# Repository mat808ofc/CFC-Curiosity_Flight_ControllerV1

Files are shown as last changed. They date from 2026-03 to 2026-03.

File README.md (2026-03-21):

# CFC (Curiosity's Flight Controller)

### About

This is a flight controller with USB-C, a Micro-SD card reader, a battery charger, servos, a pressure sensor, a IMU, a GNSS Module and voltage sensing via ADC. It was originally designed for model rockets but it can be used for planes too. I took inspiration from the @NotARoomba SFC guide, but designed it myself and this is my own creation.

### INSPIRATION:

This is my second project and first stasis project. Since I want to follow aerospace engineering, i chose to build a flight controller. I followed the @NotARoomba guide and built it from scratch. I added a GNSS Module for auto pilot and Voltage Sensing via ADC to know when the battery is getting low. I want to use this in my custom built RC plane. I really liked building everything although some things were a real pain.

### CHALLENGES:

My biggest challenge was routing the PCB, when I routed it for the first time the board was way too big to fit on the plane and way too expensive. So after that I significantly reduced the board size and made it the smallest it can get and the cheapest. In between that, I had to change a lot of pins and inputs in STM32CubeMX so that the routing wouldn't be an absolute mess, and that took a really long time and absolutely drained my patience and mental power.

### BOM:
| Name | Purpose | Cost (USD) | Qty | Total (USD) | Link | Distributor |
|---|---|---|-----|---|---|---|
| PCBA (1 board)  | The actual flight controller | $140 | 1 | $140 | https://www.elecrow.com/ | Elecrow |

Total estimated cost: $140

### Extras:

This project does not need a case or anything 3D printed or designed, it will be inside a RC plane.
If you have any questions, DM me on slack: Mateus (mateus.flecha808)

## Schematic

### USB-C & Crystals
{BE57653B-7D3A-48C3-BE49-C0519F7B529C}

### Decoupling, Buttons & Servos
{79CEA256-14AA-4DC2-861F-85EBC9C6EA1F}

### Battery Charger & STM32
{32F101CB-92D8-42CC-A244-E05E275E72F9}

### Pressure Sensor & Micro-SD
{E111CCD5-0065-440A-B6FF-7CA9D5AE25CE}

### Power & GNSS
{53D61D9F-42BA-49DF-AC49-1D3BC913D2A1}

### IMU
{816D461F-DD70-45E3-AB0F-E9185D550F2D}

### All
{09707E38-BBC4-4B8D-BA47-B80D99204EBA}

---

## PCB


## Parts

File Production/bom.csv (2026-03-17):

Designator | Footprint | Quantity | Value | LCSC Part #
C1, C3, C6, C7, C8, C9, CNEXTTOTEN1 | 0805 | 7 | 10uF
C10, C15, C18, C19, C25, C26, C27, C28, C29, C38, C42, C43, C45 | 0805 | 13 | 100nF
C11, C24 | 0402 | 2 | 2.2uF
C12, C13, C14, C16, C17 | 0805 | 5 | 22uF
C2 | 0805 | 1 | 44uF
C20 | 0805 | 1 | 10nF
C21, C23 | 0402 | 2 | 0.1uF
C22 | 0402 | 1 | 2.2nF
C30, C31, C32, C33, C44 | 0402 | 5 | 1uF
C34, C35 | 0805 | 2 | 20pF
C36, C37 | 0402 | 2 | 6.8pF
C4 | 0805 | 1 | 1uF
C5 | 0805 | 1 | 47nF
CARD1 | TF-SMD_TF-01A | 1 | TF-01A | C91145
D1 | 0402 | 1 | LED
J1 | TerminalBlock_Xinya_XY308-2.54-2P_1x02_P2.54mm_Horizontal | 1 | Screw_Terminal_01x02
J2, J3 | PinHeader_1x03_P2.54mm_Vertical | 2 | Conn_01x03
L1 | L2520 | 1 | 1uH
L2 | IND-SMD_L4.0-W4.0-A | 1 | 1.5uH
L3 | IND-SMD_L3.0-W3.0 | 1 | 5.6uH
L4 | L0603 | 1 | FCM1608KF-601T03 | C141723
R1, R2 | 0402 | 2 | 5.1K
R10, R12, R13, R16, R17, R18, R19, R20, R21, R24, R27, R3, R4, R5, R6, R7 | 0402 | 16 | 10K
R11 | 0402 | 1 | 30.1K
R14 | 0402 | 1 | 100K
R15 | 0402 | 1 | 22.1K
R22, R23 | 0402 | 2 | 4.7K
R25 | 0805 | 1 | 200K
R26 | 0805 | 1 | 100K
R8 | 0402 | 1 | 383
R9 | 0402 | 1 | 5.23K
SW1, SW2 | SW-SMD_L3.9-W3.0-P4.45 | 2 | TS-1088-AR02016 | C720477
U1 | VFQFPN-24_L4.0-W4.0-P0.50-BL-EP2.8 | 1 | BQ25883RGER | C544362
U2 | LQFP-64_10x10mm_P0.5mm | 1 | STM32F722RET6
U3 | InvenSense_QFN-24_4x4mm_P0.5mm | 1 | MPU-6050
U4 | VQFN-15_L3.0-W2.5-P0.50-BL | 1 | TPS63070RNMR | C109322
U5 | SOT-23-6 | 1 | LMR51430
U6 | LGA-10_L2.0-W2.0-P0.50-TL_BMP580 | 1 | BMP580 | C22391138
U8 | ublox_SAM-M8Q | 1 | SAM-M8Q
USB1 | USB-C-SMD_TYPE-C-6PIN-2MD-073 | 1 | TYPE-C 16PIN 2MD(073) | C2765186
X1 | CRYSTAL-SMD_4P-L3.2-W2.5-BL | 1 | X322525MOB4SI | C9006
X2 | FC-135R_L3.2-W1.5 | 1 | Q13FC1350000400 | C32346

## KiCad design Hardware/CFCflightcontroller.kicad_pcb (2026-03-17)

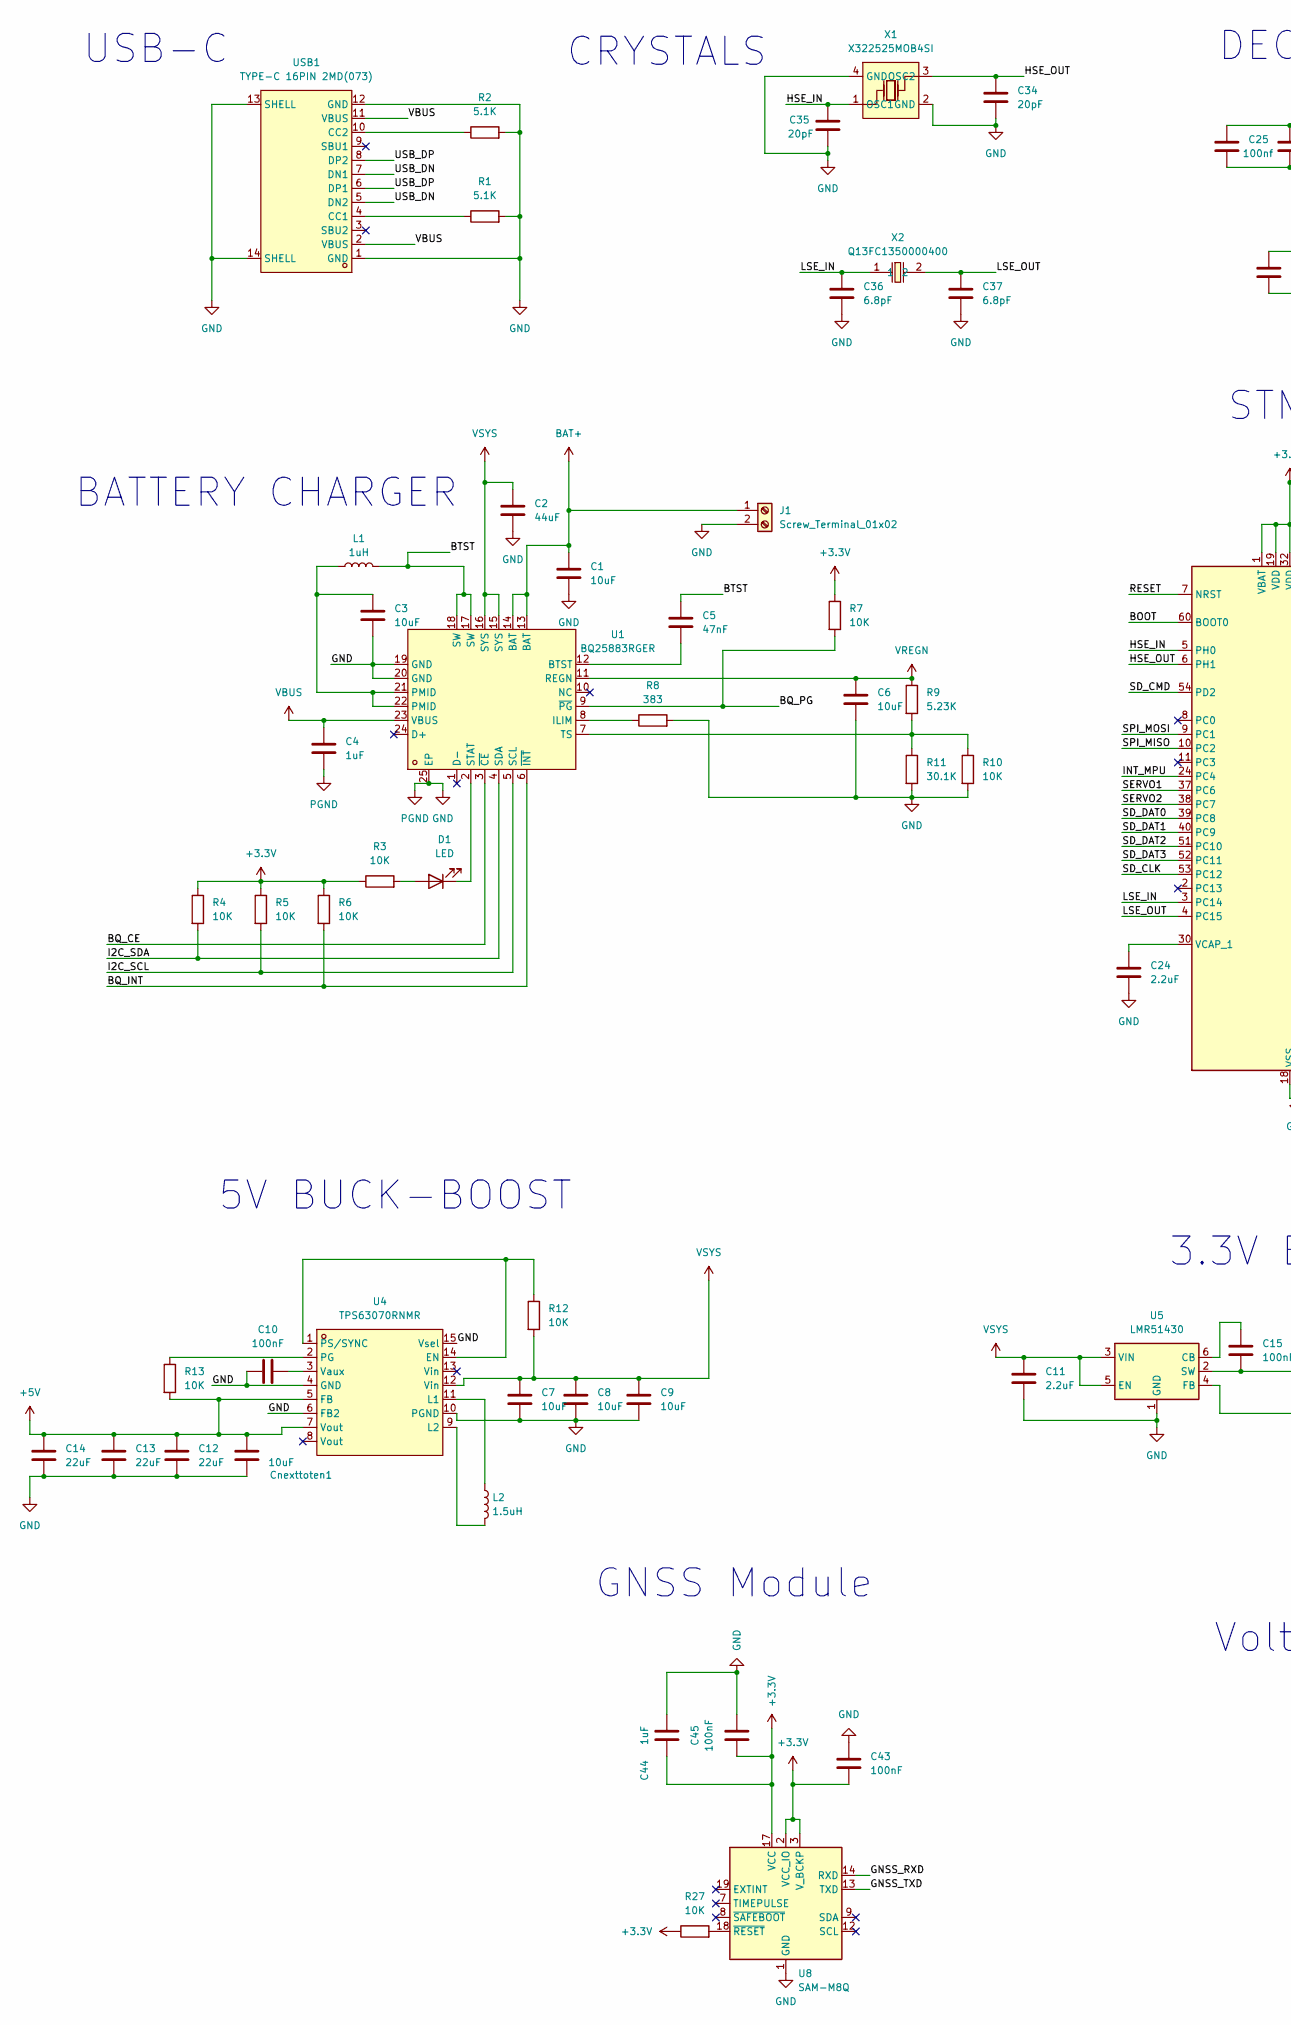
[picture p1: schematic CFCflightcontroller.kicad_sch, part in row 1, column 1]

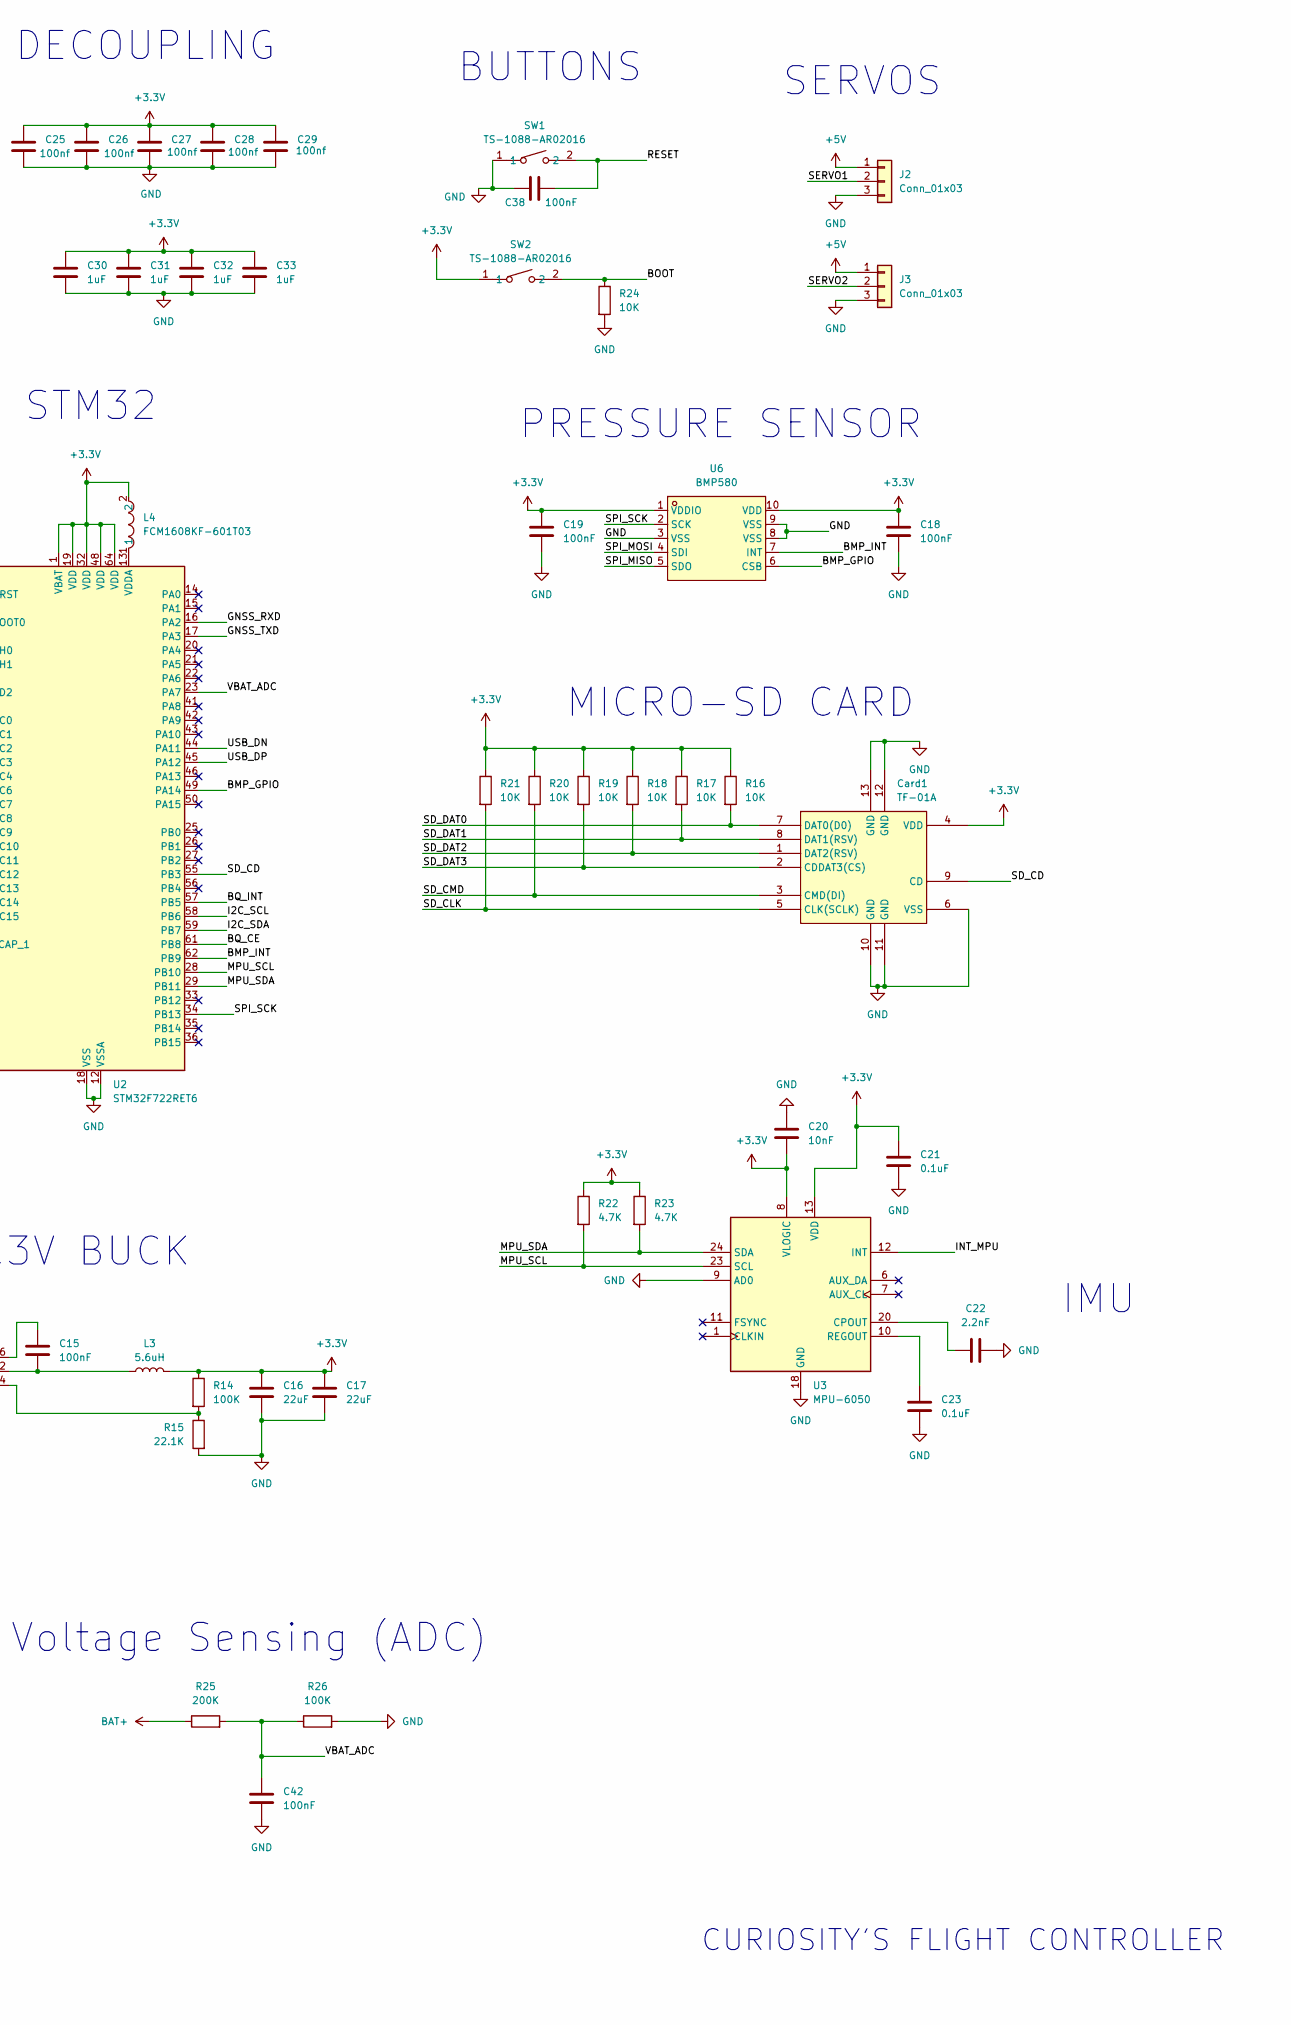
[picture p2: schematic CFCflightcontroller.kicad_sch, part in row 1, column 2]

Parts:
C1, C3, C6, C7, C8, C9: 10uF; C_0805_2012Metric
C2: 44uF; C_0805_2012Metric
C4: 1uF; C_0805_2012Metric
C5: 47nF; C_0805_2012Metric
C10, C15, C18, C19, C38, C42, C43, C45: 100nF; C_0805_2012Metric
C11, C24: 2.2uF; C_0402_1005Metric
C12, C13, C14, C16, C17: 22uF; C_0805_2012Metric
C20: 10nF; C_0805_2012Metric
C21, C23: 0.1uF; C_0402_1005Metric
C22: 2.2nF; C_0402_1005Metric
C25, C26, C27, C28, C29: 100nf; C_0805_2012Metric
C30, C31, C32, C33, C44: 1uF; C_0402_1005Metric
C34, C35: 20pF; C_0805_2012Metric
C36, C37: 6.8pF; C_0402_1005Metric
Card1: TF-01A; TF-SMD_TF-01A; LCSC Part C91145
Cnexttoten1: 10uF; C_0805_2012Metric
D1: LED; LED_0402_1005Metric
J1: Screw_Terminal_01x02; TerminalBlock_Xinya_XY308-2.54-2P_1x02_P2.54mm_Horizontal
J2, J3: Conn_01x03; PinHeader_1x03_P2.54mm_Vertical
L1: 1uH; L2520
L2: 1.5uH; IND-SMD_L4.0-W4.0-A
L3: 5.6uH; IND-SMD_L3.0-W3.0
L4: FCM1608KF-601T03; L0603; LCSC Part C141723
R1, R2: 5.1K; R_0402_1005Metric
R3, R4, R5, R6, R7, R10, R12, R13, R16, R17, R18, R19, R20, R21, R24, R27: 10K; R_0402_1005Metric
R8: 383; R_0402_1005Metric
R9: 5.23K; R_0402_1005Metric
R11: 30.1K; R_0402_1005Metric
R14: 100K; R_0402_1005Metric
R15: 22.1K; R_0402_1005Metric
R22, R23: 4.7K; R_0402_1005Metric
R25: 200K; R_0805_2012Metric
R26: 100K; R_0805_2012Metric
SW1, SW2: TS-1088-AR02016; SW-SMD_L3.9-W3.0-P4.45; LCSC Part C720477
U1: BQ25883RGER; VFQFPN-24_L4.0-W4.0-P0.50-BL-EP2.8; LCSC Part C544362
U2: STM32F722RET6; LQFP-64_10x10mm_P0.5mm
U3: MPU-6050; InvenSense_QFN-24_4x4mm_P0.5mm
U4: TPS63070RNMR; VQFN-15_L3.0-W2.5-P0.50-BL; LCSC Part C109322
U5: LMR51430; SOT-23-6
U6: BMP580; LGA-10_L2.0-W2.0-P0.50-TL_BMP580; LCSC Part C22391138
U8: SAM-M8Q; ublox_SAM-M8Q
USB1: TYPE-C 16PIN 2MD(073); USB-C-SMD_TYPE-C-6PIN-2MD-073; LCSC Part C2765186
X1: X322525MOB4SI; CRYSTAL-SMD_4P-L3.2-W2.5-BL; LCSC Part C9006
X2: Q13FC1350000400; FC-135R_L3.2-W1.5; LCSC Part C32346

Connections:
+3.3V: C16.1, C17.1, C18.1, C19.1, C20.2, C21.1, C25.1, C26.1, C27.1, C28.1, C29.1, C30.1, C31.1, C32.1, C33.1, C43.1, C44.1, C45.1, Card1.4 (VDD), L3.2, L4.2, R3.1, R4.1, R5.1, R6.1, R7.1, R14.1, R16.1, R17.1, R18.1, R19.1, R20.1, R21.1, R22.1, R23.1, R27.1, SW2.1, U2.1 (VBAT), U2.19 (VDD), U2.32 (VDD), U2.48 (VDD), U2.64 (VDD), U3.8 (VLOGIC), U3.13 (VDD), U6.1 (VDDIO), U6.10 (VDD), U8.2 (VCC_IO), U8.3 (V_BCKP), U8.17 (VCC)
+5V: C12.1, C13.1, C14.1, Cnexttoten1.1, J2.1, J3.1, R13.2, U4.5 (FB), U4.7 (Vout)
/BMP_GPIO: U2.49 (PA14), U6.6 (CSB)
/BMP_INT: U2.62 (PB9), U6.7 (INT)
/BOOT: R24.1, SW2.2, U2.60 (BOOT0)
/BQ_CE: U1.3 (~CE), U2.61 (PB8)
/BQ_INT: R6.2, U1.6 (~INT), U2.57 (PB5)
/BQ_PG: R7.2, U1.9 (~PG)
/BTST: C5.1, L1.2, U1.17 (SW), U1.18 (SW)
/GNSS_RXD: U2.16 (PA2), U8.14 (RXD)
/GNSS_TXD: U2.17 (PA3), U8.13 (TXD)
/HSE_IN: C35.1, U2.5 (PH0), X1.1 (OSC1)
/HSE_OUT: C34.1, U2.6 (PH1), X1.3 (OSC2)
/I2C_SCL: R5.2, U1.5 (SCL), U2.58 (PB6)
/I2C_SDA: R4.2, U1.4 (SDA), U2.59 (PB7)
/INT_MPU: U2.24 (PC4), U3.12 (INT)
/LSE_IN: C36.1, U2.3 (PC14), X2.1
/LSE_OUT: C37.1, U2.4 (PC15), X2.2
/MPU_SCL: R22.2, U2.28 (PB10), U3.23 (SCL)
/MPU_SDA: R23.2, U2.29 (PB11), U3.24 (SDA)
/RESET: C38.2, SW1.2, U2.7 (NRST)
/SD_CD: Card1.9 (CD), U2.55 (PB3)
/SD_CLK: Card1.5 (CLK(SCLK)), R21.2, U2.53 (PC12)
/SD_CMD: Card1.3 (CMD(DI)), R20.2, U2.54 (PD2)
/SD_DAT0: Card1.7 (DAT0(D0)), R16.2, U2.39 (PC8)
/SD_DAT1: Card1.8 (DAT1(RSV)), R17.2, U2.40 (PC9)
/SD_DAT2: Card1.1 (DAT2(RSV)), R18.2, U2.51 (PC10)
/SD_DAT3: Card1.2 (CDDAT3(CS)), R19.2, U2.52 (PC11)
/SERVO1: J2.2, U2.37 (PC6)
/SERVO2: J3.2, U2.38 (PC7)
/SPI_MISO: U2.10 (PC2), U6.5 (SDO)
/SPI_MOSI: U2.9 (PC1), U6.4 (SDI)
/SPI_SCK: U2.34 (PB13), U6.2 (SCK)
/USB_DN: U2.44 (PA11), USB1.5 (DN2), USB1.7 (DN1)
/USB_DP: U2.45 (PA12), USB1.6 (DP1), USB1.8 (DP2)
/VBAT_ADC: C42.1, R25.2, R26.1, U2.23 (PA7)
BAT+: C1.1, J1.1, R25.1, U1.13 (BAT), U1.14 (BAT)
GND: C1.2, C2.2, C3.2, C4.2, C6.2, C7.2, C8.2, C9.2, C10.1, C11.2, C12.2, C13.2, C14.2, C16.2, C17.2, C18.2, C19.2, C20.1, C21.2, C22.2, C23.2, C24.2, C25.2, C26.2, C27.2, C28.2, C29.2, C30.2, C31.2, C32.2, C33.2, C34.2, C35.2, C36.2, C37.2, C38.1, C42.2, C43.2, C44.2, C45.2, Card1.6 (VSS), Card1.10 (GND), Card1.11 (GND), Card1.12 (GND), Card1.13 (GND), Cnexttoten1.2, J1.2, J2.3, J3.3, R1.2, R2.2, R8.2, R10.2, R11.2, R15.2, R24.2, R26.2, SW1.1, U1.19 (GND), U1.20 (GND), U1.25 (EP), U2.12 (VSSA), U2.18 (VSS), U2.31 (VSS), U2.47 (VSS), U2.63 (VSS), U3.9 (AD0), U3.18 (GND), U4.4 (GND), U4.6 (FB2), U4.10 (PGND), U4.15 (Vsel), U5.1 (GND), U6.3 (VSS), U6.8 (VSS), U6.9 (VSS), U8.1 (GND), U8.4 (GND), U8.5 (GND), U8.6 (GND), U8.10 (GND), U8.11 (GND), U8.15 (GND), U8.16 (GND), U8.20 (GND), USB1.1 (GND), USB1.12 (GND), USB1.13 (SHELL), USB1.14 (SHELL), X1.2 (GND), X1.4 (GND)
unnamed: C3.1, L1.1, U1.21 (PMID), U1.22 (PMID)
unnamed: D1.2 (A), R3.2
unnamed: D1.1 (K), U1.2 (STAT)
unnamed: C5.2, U1.12 (BTST)
unnamed: R8.1, U1.8 (ILIM)
unnamed: R9.2, R10.1, R11.1, U1.7 (TS)
unnamed: C24.1, U2.30 (VCAP_1)
unnamed: L4.1, U2.13 (VDDA)
unnamed: C22.1, U3.20 (CPOUT)
unnamed: C23.1, U3.10 (REGOUT)
unnamed: R12.1, U4.1 (PS/SYNC), U4.14 (EN)
unnamed: L2.1, U4.11 (L1)
unnamed: L2.2, U4.9 (L2)
unnamed: R13.1, U4.2 (PG)
unnamed: C10.2, U4.3 (Vaux)
unnamed: C15.1, U5.6 (CB)
unnamed: R14.2, R15.1, U5.4 (FB)
unnamed: C15.2, L3.1, U5.2 (SW)
unnamed: R27.2, U8.18 (~RESET)
unnamed: R1.1, USB1.4 (CC1)
unnamed: R2.1, USB1.10 (CC2)
VBUS: C4.1, U1.23 (VBUS), USB1.2 (VBUS), USB1.11 (VBUS)
VREGN: C6.1, R9.1, U1.11 (REGN)
VSYS: C2.1, C7.1, C8.1, C9.1, C11.1, R12.2, U1.15 (SYS), U1.16 (SYS), U4.12 (Vin), U5.3 (VIN), U5.5 (EN)

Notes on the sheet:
DECOUPLING
CURIOSITY'S FLIGHT CONTROLLER
5V BUCK-BOOST
MICRO-SD CARD
CRYSTALS
USB-C
BUTTONS
IMU
Voltage Sensing (ADC)
PRESSURE SENSOR
BATTERY CHARGER
SERVOS
GNSS Module
3.3V BUCK
STM32

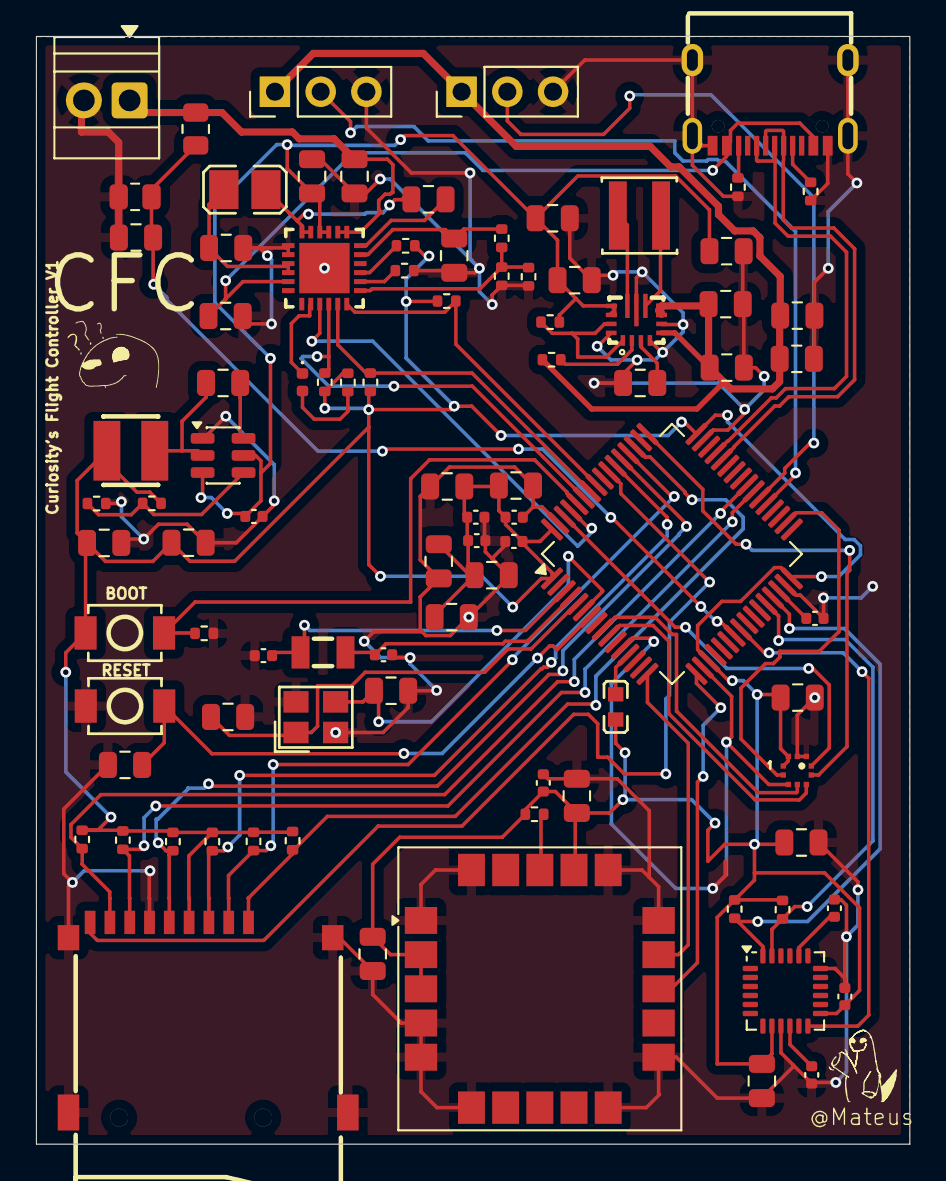
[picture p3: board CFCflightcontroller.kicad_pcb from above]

Board: 2 copper layers, 48.5 x 61.5 mm, 91 parts (0 on the bottom side), 62 nets.

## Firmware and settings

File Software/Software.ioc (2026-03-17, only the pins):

Mcu.UserName=STM32F722RETx
PA11.Signal=USB_OTG_FS_DM
PA12.Signal=USB_OTG_FS_DP
PA14.Signal=GPIO_Output
PA2.Signal=USART2_TX
PA3.Signal=USART2_RX
PA7.Signal=ADCx_IN7
PB10.Signal=I2C2_SCL
PB11.Signal=I2C2_SDA
PB13.Signal=SPI2_SCK
PB3.Signal=GPIO_Input
PB5.Signal=GPXTI5
PB6.Signal=I2C1_SCL
PB7.Signal=I2C1_SDA
PB8.Signal=GPIO_Output
PC1.Signal=SPI2_MOSI
PC10.Signal=SDMMC1_D2
PC11.Signal=SDMMC1_D3
PC12.Signal=SDMMC1_CK
PC14-OSC32_IN.Signal=RCC_OSC32_IN
PC15-OSC32_OUT.Signal=RCC_OSC32_OUT
PC2.Signal=SPI2_MISO
PC4.Signal=GPXTI4
PC6.Signal=S_TIM3_CH1
PC7.Signal=S_TIM3_CH2
PC8.Signal=SDMMC1_D0
PC9.Signal=SDMMC1_D1
PD2.Signal=SDMMC1_CMD
PH0-OSC_IN.Signal=RCC_OSC_IN
PH1-OSC_OUT.Signal=RCC_OSC_OUT

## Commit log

2026-03-16 Enhance README with project details and images
    Added detailed project description, BOM, and images.
2026-03-17 Add note about unpredictable PCBA costs
    Added an important note regarding component costs and procurement uncertainties.
2026-03-21 Revise BOM and total cost in README
    Updated BOM with new pricing and supplier information.
